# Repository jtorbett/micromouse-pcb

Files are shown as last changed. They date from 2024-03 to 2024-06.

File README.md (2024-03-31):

# Micromouse code

*A maze-solving micromouse implemented on STM32F446RE*

This mouse design has two DC motors driven by a TI DRV8833, and 4 IR sensors, two looking forward at an outward angle and two looking sideways, again at an angle.
Odometry is provided by a hall effect quadrature encoder on each motor.
Provision is made for a TDK ICM-42688 IMU, or a TDK ICM-45688 if and when that becomes available.
A forward-facing VL53L4CD time-of-flight ranging sensor is used for look-ahead

## Pin Descriptions

| STM32F446RE Pin number | Configuration | Name | Description |
|---|---|---|---|
| | PWM Output | LMotor_A | Left motor PWM signal 1 |
| | PWM Output | LMotor_B | Left motor PWM signal 2 |
| | PWM Output | RMotor_A | Right motor PWM signal 1 |
| | PWM Output | RMotor_B | Right motor PWM signal 2 |
| | GPIO Output | Motors_EN | DRM8833 Enable line |
| | GPIO Output | IR_Front_L_Pulse | Front left IR emitter pulse enable |
| | GPIO Output | IR_Front_R_Pulse | Front right IR emitter pulse enable |
| | GPIO Output | IR_L_Pulse | Left IR emitter pulse enable |
| | GPIO Output | IR_R_Pulse | Right IR emitter pulse enable |
| | ADC | IR_Front_L | Front Left IR Sensor |
| | ADC | IR_Front_R | Front Right IR Sensor |
| | ADC | IR_L | Left IR Sensor |
| | ADC | IR_R | Right IR Sensor |
| | Interrupt Input | L_ENC_A | Left encoder channel A |
| | Interrupt Input | L_ENC_B | Left encoder channel B |
| | Interrupt Input | R_ENC_A | Right encoder channel A |
| | Interrupt Input | R_ENC_B | Right encoder channel B |
| | I2C SDA | VL53L4CD_SDA | I2C bus data for VL53L4CD |
| | I2C SCL | VL53L4CD_SCL | I2C bus clock for VL53L4CD |
| | Interrupt Input | VL53L4CD_INT | Interrupt from VL53L4CD |
| | GPIO Output | VL53L4CD_EN | Enable for VL53L4CD |
| | SPI SCK | ICM-42688_SCK | SPI Clock for ICM-42688 |
| | SPI MISO | ICM-42688_MISO | SPI MISO for ICM-42688 |
| | SPI MOSI | ICM-42688_MOSI | SPI MOSI for ICM-42688 |
| | SPI CS or GPIO Output | ICM-42688_CS | Chip select, active low, for ICM-42688 |
| | GPIO Interrupt | ICM-42688_INT1 | Interrupt 1 from ICM-42688 |
| | GPIO Interrupt | ICM-42688_INT2 | Interrupt 2 from ICM-42688 |
| | GPIO Input or Interrupt | SW1 | Switch 1, momentary push-button input |
| | GPIO Input or Interrupt | SW2 | Switch 2, momentary push-button input |
| | GPIO Output | LED1 | LED 1 Output |
| | GPIO Output | LED2 | LED 2 Output |
| | ADC | VBATT | Battery voltage input |
| | SWDIO | SWDIO | Serial Wire Debug Data |
| | SWDCLK | SWDCLK | Serial Wire Debug Clock |

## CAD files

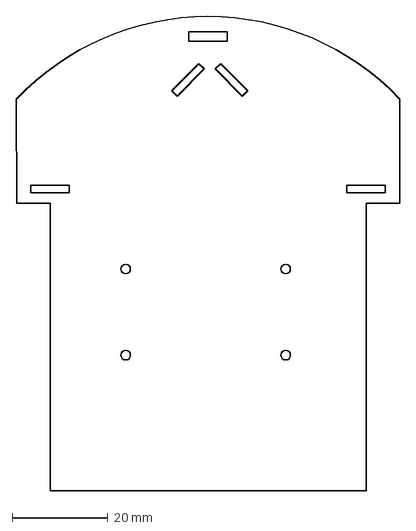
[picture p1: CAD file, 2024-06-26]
micromouse-pcb/outline.dxf
80.0 x 99.0 mm

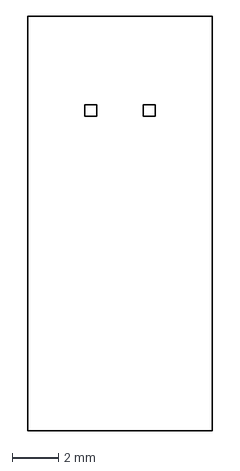
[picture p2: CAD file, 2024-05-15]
micromouse-pcb/sensor-outline.dxf
8.00 x 18.0 mm

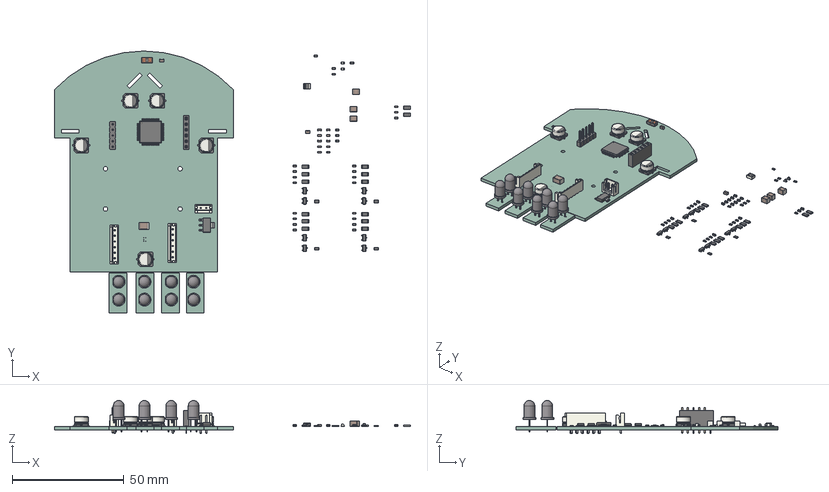
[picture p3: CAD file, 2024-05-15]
micromouse-pcb/micromouse-pcb.step
159.4 x 117.3 x 14.8 mm
SOT_23 x 8
R_0603_1608Metric x 21
R_1206_3216Metric x 14
CP_Elec_63x45 x 5
C_0603_1608Metric x 15
R_0805_2012Metric x 4
ST_VL53L1x
C_1210_3225Metric x 3
LED_D5.0mm_IRGrey x 8
PinHeader_1x05_P254mm_Vertical
Fuse_1210_3225Metric
LED_0603_1608Metric x 2
C_0805_2012Metric x 2
LQFP_64_10x10mm_P05mm
C_1812_4532Metric
JST_B2B_EH_A
SOT_223
JST_B6B_EH_A x 2
PinSocket_1x06_P254mm_Vertical
_autosave-micromouse-pcb_PCB_1
_autosave-micromouse-pcb_PCB_2
_autosave-micromouse-pcb_PCB_3
_autosave-micromouse-pcb_PCB_4
_autosave-micromouse-pcb_PCB_5

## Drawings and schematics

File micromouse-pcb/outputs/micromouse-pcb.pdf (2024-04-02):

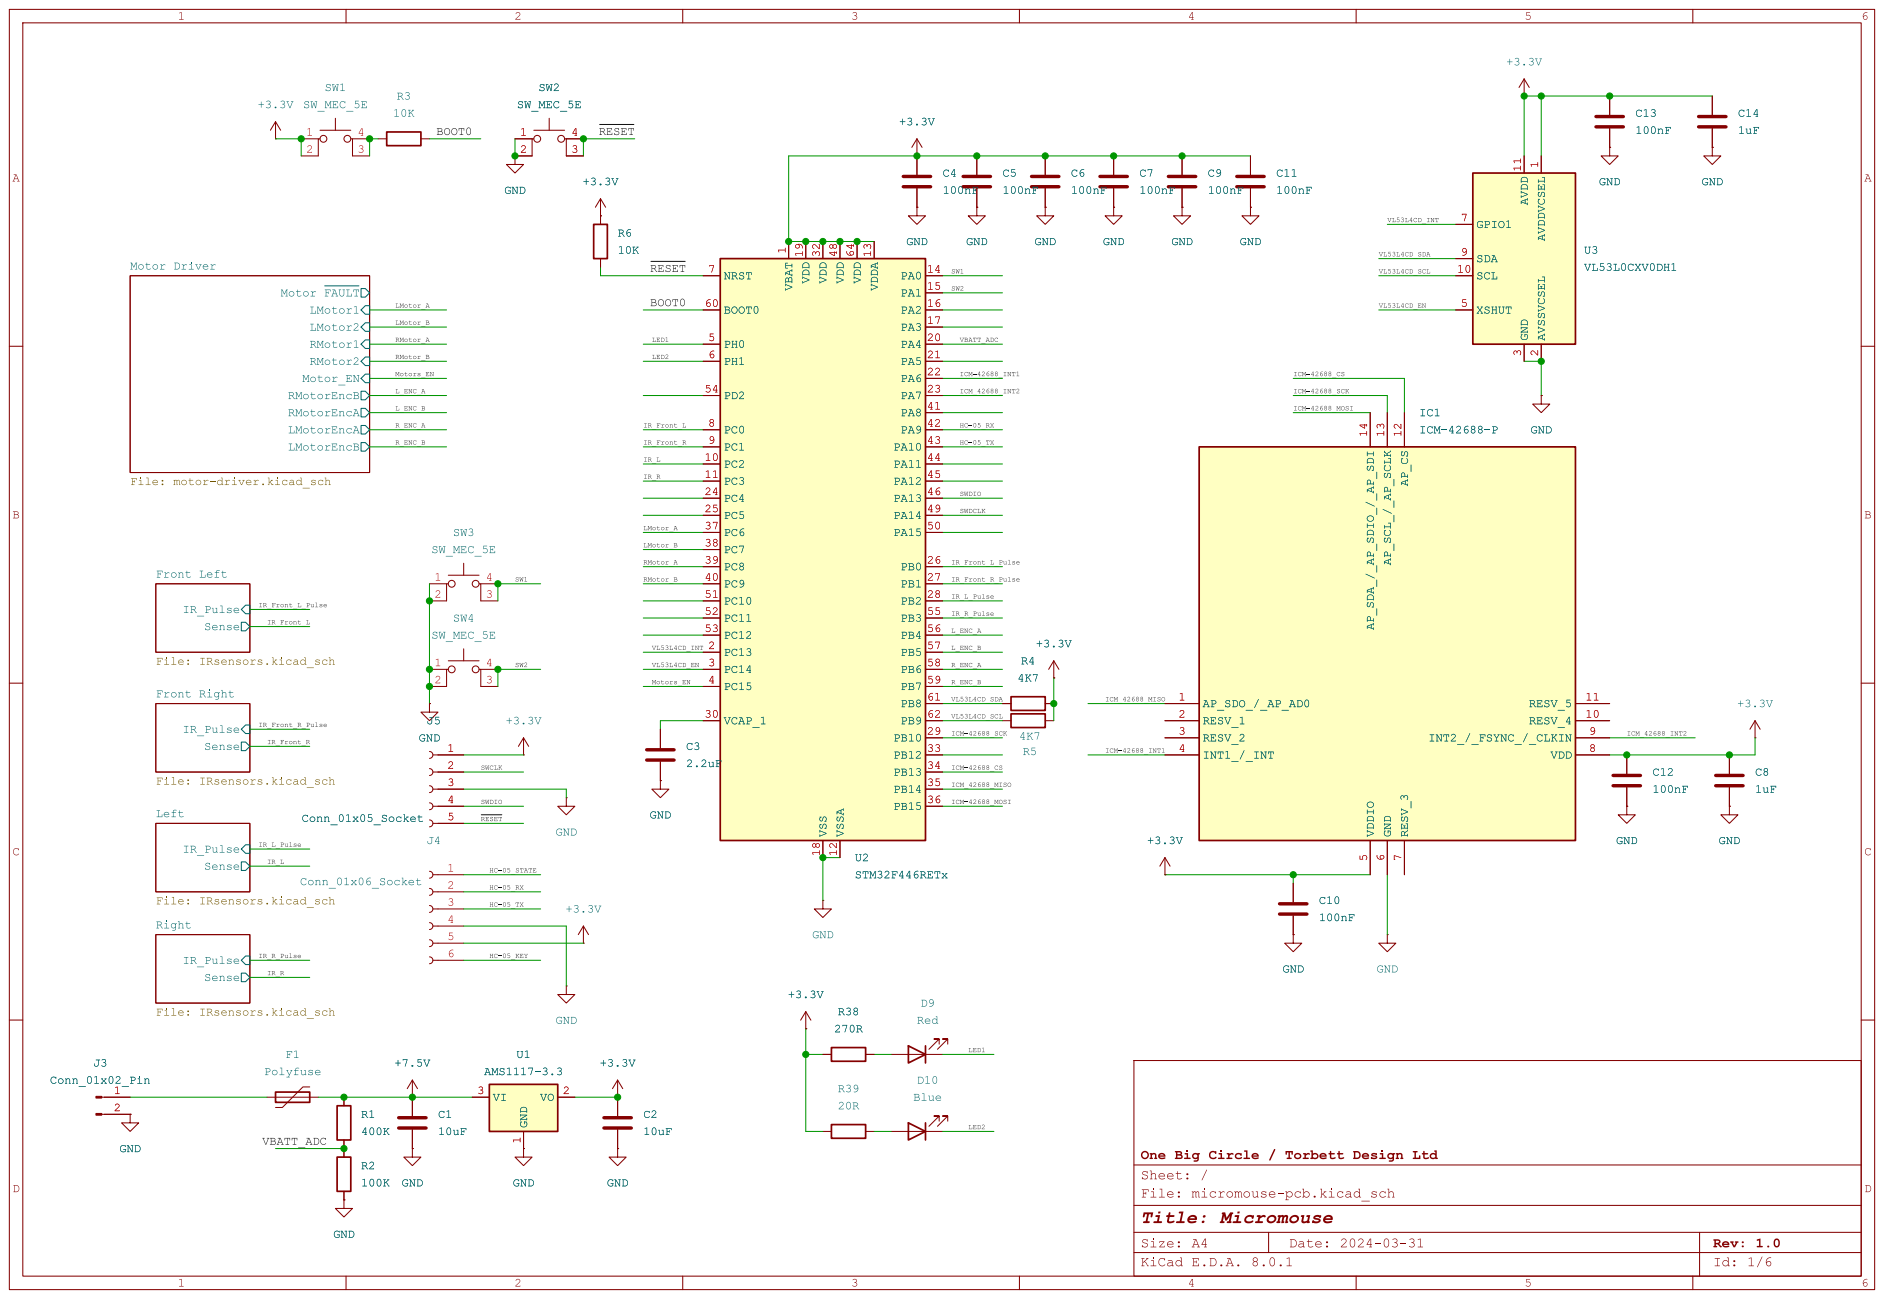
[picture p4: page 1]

1 PC2 10 PC3 11 VSSA 12 VDDA13 PA0 14 PA1 15 PA2 16 PA3 17 VSS 18 VDD19 PC13 2 PA4 20 PA5 21 PA6 22 PA7 23 PC4 24 PC5 25 PB0 26 PB1 27 PB2 28 PB10 29 PC14 3 VCAP_1 30 VDD32 PB12 33 PB13 34 PB14 35 PB15 36 PC6 37 PC7 38 PC8 39 PC15 4 PC9 40 PA8 41 PA9 42 PA10 43 PA11 44 PA12 45 PA13 46 VDD48 PA14 49 PH0 5 PA15 50 PC10 51 PC11 52 PC12 53 PD2 54 PB3 55 PB4 56 PB5 57 PB6 58 PB7 59 PH1 6 BOOT0 60 PB8 61 PB9 62 VDD64 NRST 7 PC0 8 PC1 9 GND
IR_L ~{RESET}

1 PC2 10 PC3 11 VSSA 12 VDDA13 PA0 14 PA1 15 PA2 16 PA3 17 VSS 18 VDD19 PC13 2 PA4 20 PA5 21 PA6 22 PA7 23 PC4 24 PC5 25 PB0 26 PB1 27 PB2 28 PB10 29 PC14 3 VCAP_1 30 VDD32 PB12 33 PB13 34 PB14 35 PB15 36 PC6 37 PC7 38 PC8 39 PC15 4 PC9 40 PA8 41 PA9 42 PA10 43 PA11 44 PA12 45 PA13 46 VDD48 PA14 49 PH0 5 PA15 50 PC10 51 PC11 52 PC12 53 PD2 54 PB3 55 PB4 56 PB5 57 PB6 58 PB7 59 PH1 6 BOOT0 60 PB8 61 PB9 62 VDD64 NRST 7 PC0 8 PC1 9 U2STM32F446RETx GND

ICM-42688_MOSI HC-05_STATE HC-05_RX HC-05_KEY

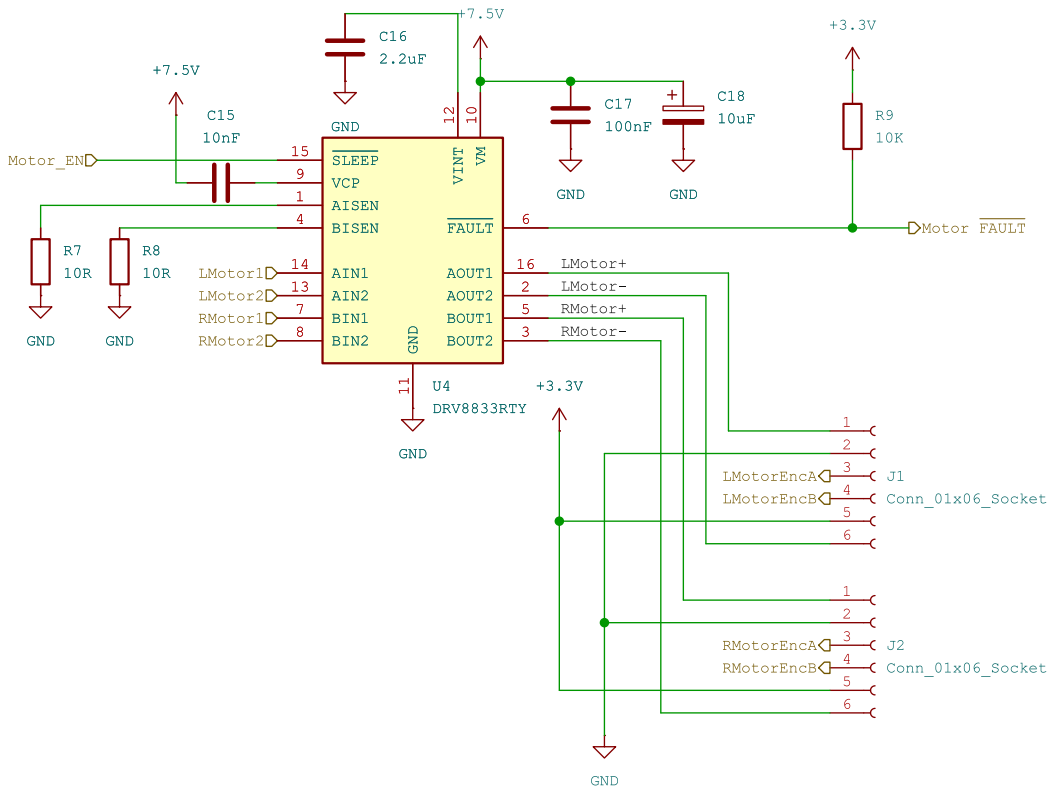
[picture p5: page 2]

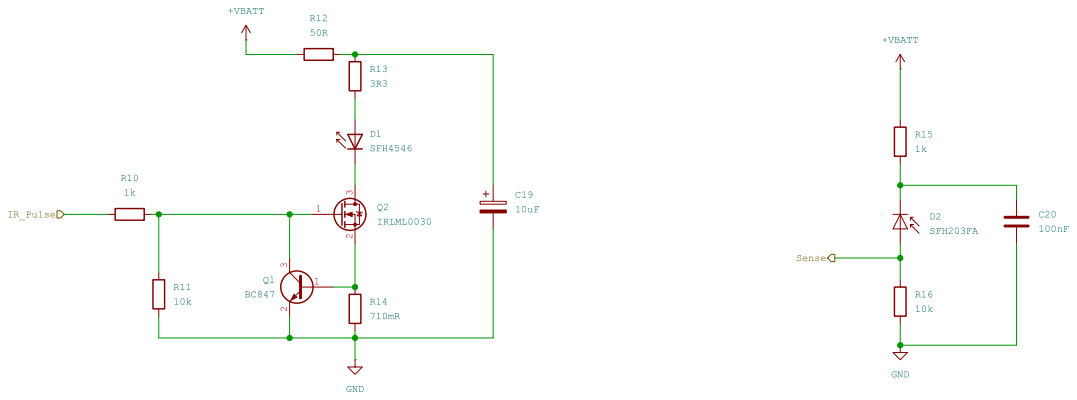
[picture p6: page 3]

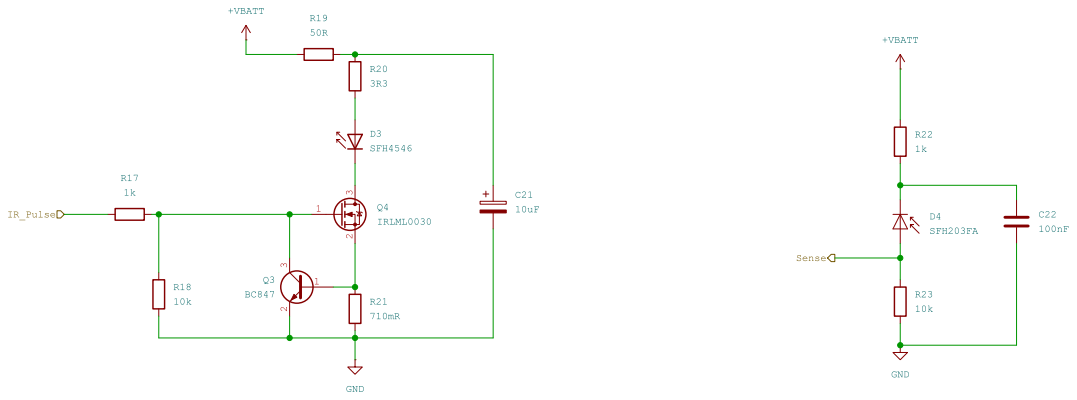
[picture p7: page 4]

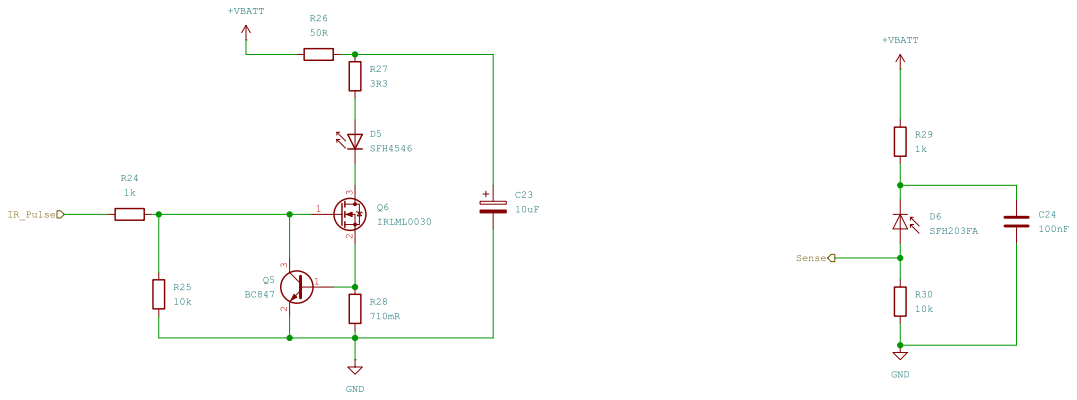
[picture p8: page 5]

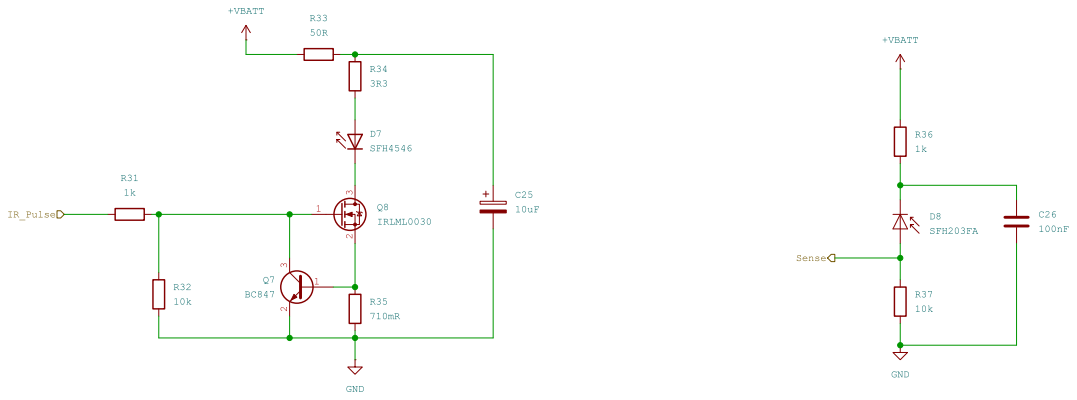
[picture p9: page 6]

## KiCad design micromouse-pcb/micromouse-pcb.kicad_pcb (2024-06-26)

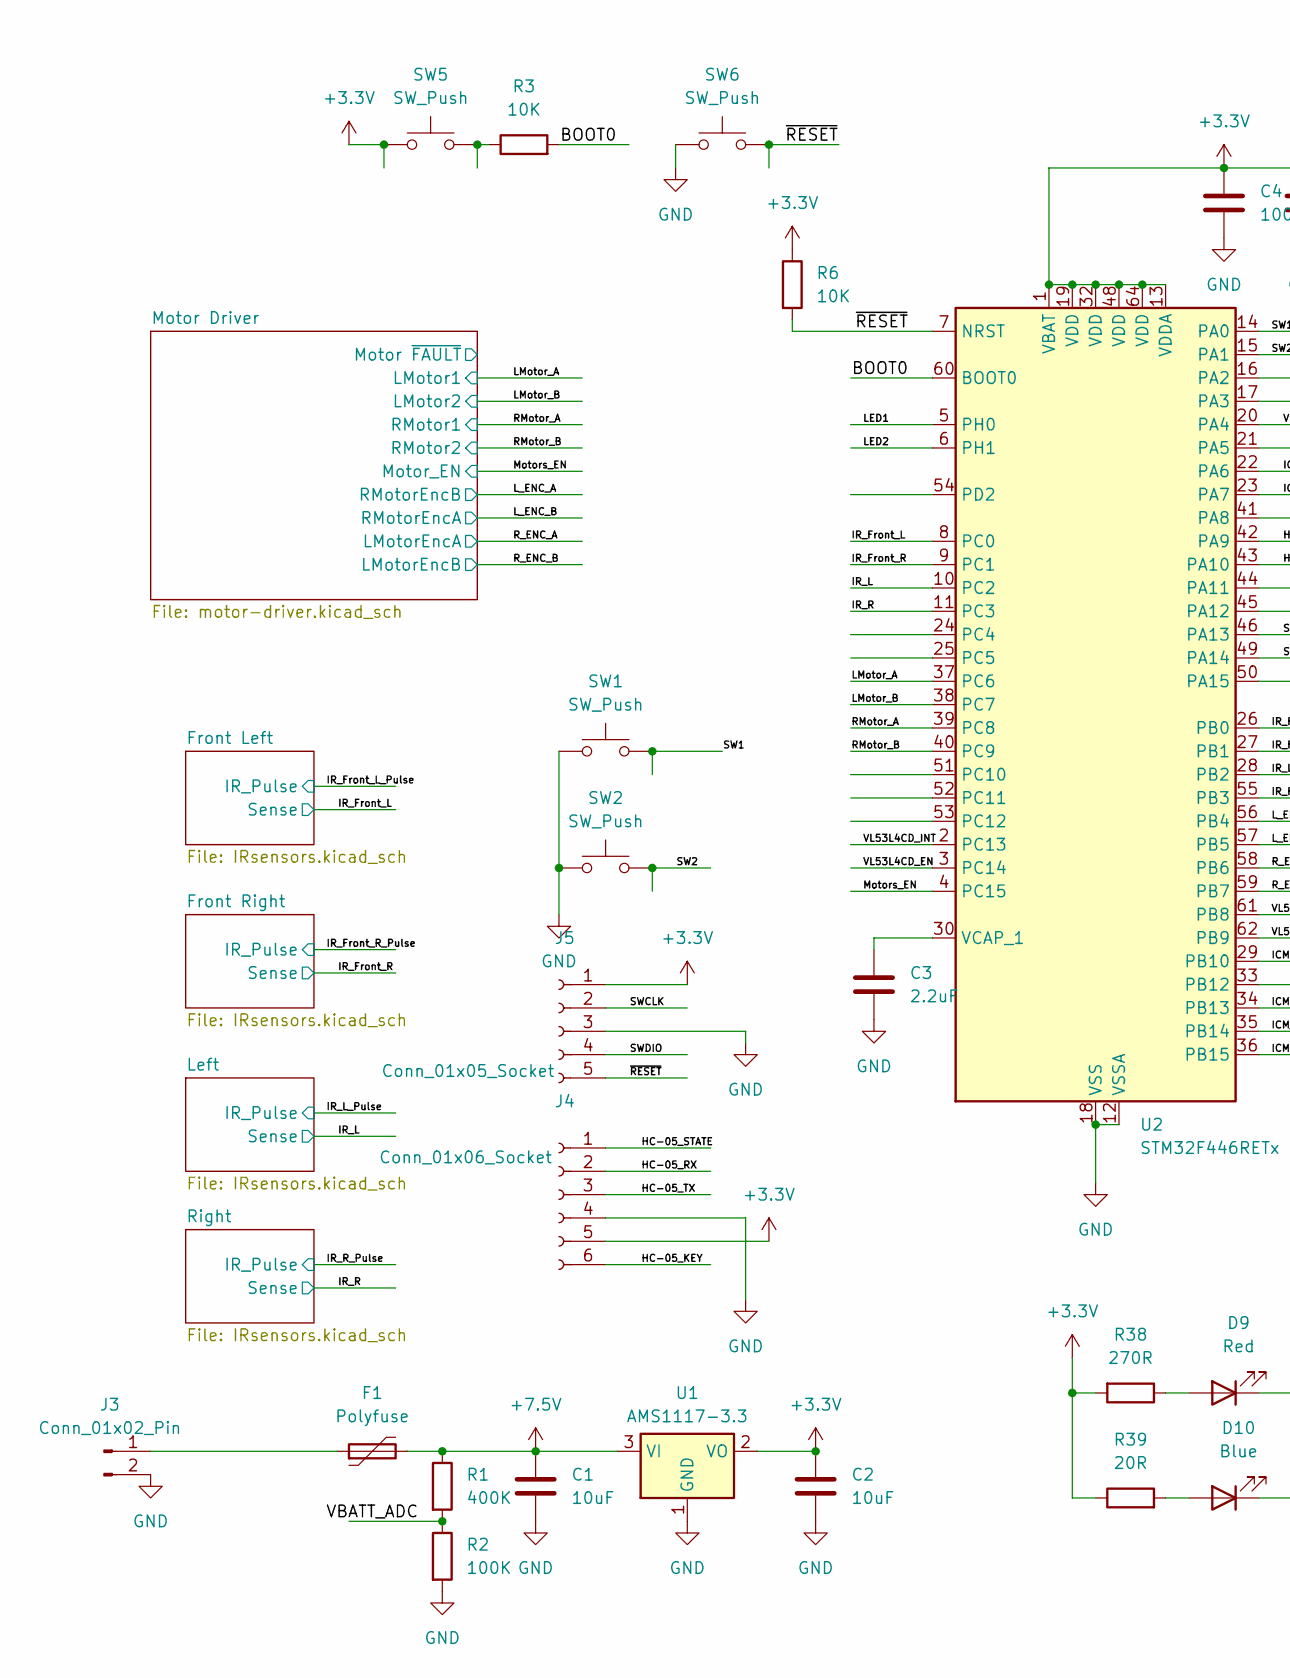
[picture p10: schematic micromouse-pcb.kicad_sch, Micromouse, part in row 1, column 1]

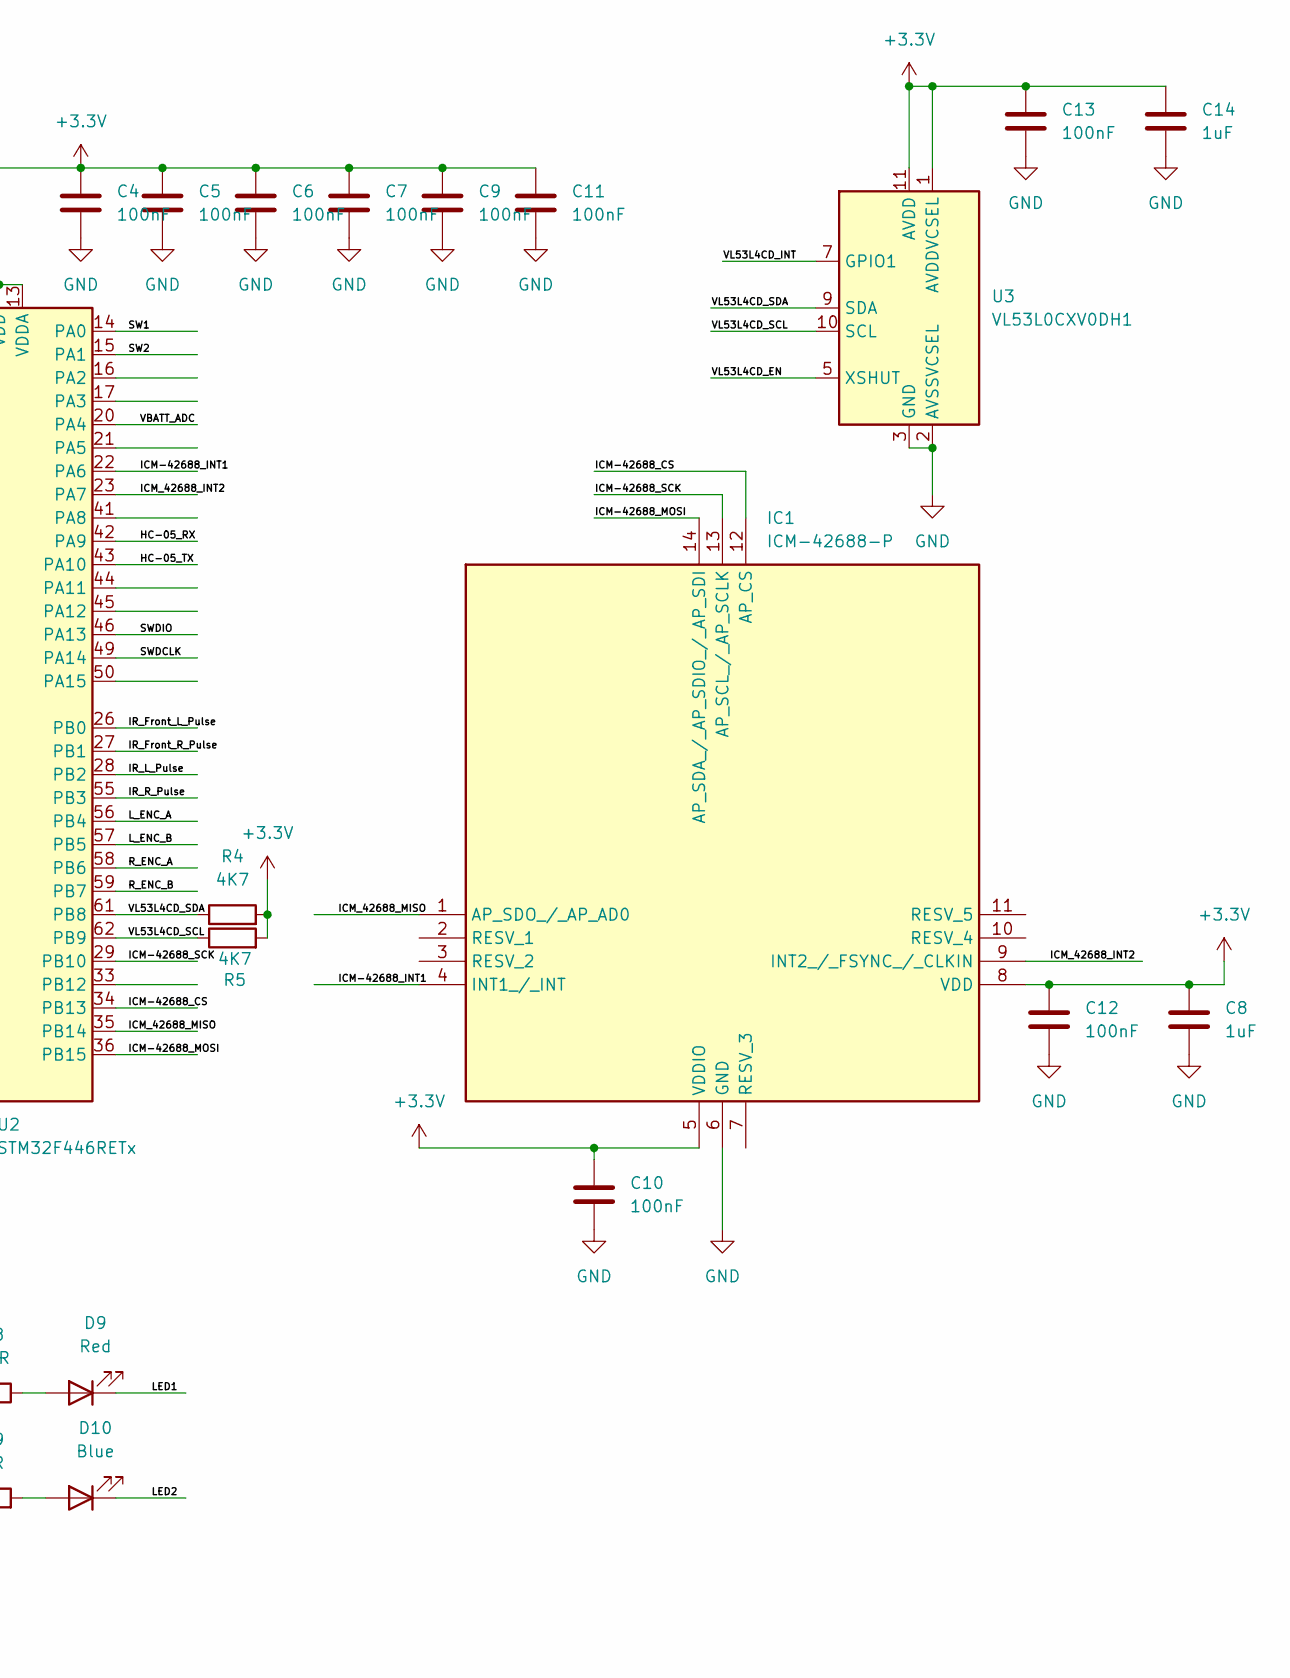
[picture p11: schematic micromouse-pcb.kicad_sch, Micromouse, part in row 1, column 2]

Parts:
C1, C2: 10uF; C_1210_3225Metric
C3: 2.2uF; C_1210_3225Metric
C4, C5, C6, C7, C9, C11, C12, C13: 100nF; C_0603_1608Metric
C8: 1uF; C_0603_1608Metric
C10: 100nF; C_0805_2012Metric
C14: 1uF; C_0805_2012Metric
D9: Red; LED_0603_1608Metric
D10: Blue; LED_0603_1608Metric
F1: Polyfuse; Fuse_1210_3225Metric
IC1: ICM-42688-P; IIM42352; Mouser Part Number 410-ICM-42688-P
J3: Conn_01x02_Pin; JST_EH_B2B-EH-A_1x02_P2.50mm_Vertical
J4: Conn_01x06_Socket; PinSocket_1x06_P2.54mm_Vertical
J5: Conn_01x05_Socket; PinHeader_1x05_P2.54mm_Vertical
R1: 400K; R_0603_1608Metric
R2: 100K; R_0603_1608Metric
R3, R6: 10K; R_0603_1608Metric
R4, R5: 4K7; R_0603_1608Metric
R38: 270R; R_0603_1608Metric_Pad0.98x0.95mm_HandSolder
R39: 20R; R_0603_1608Metric
SW1, SW2, SW5, SW6: SW_Push; SW_Push_1P1T_NO_CK_KSC6xxJ
U1: AMS1117-3.3; SOT-223-3_TabPin2
U2: STM32F446RETx; LQFP-64_10x10mm_P0.5mm
U3: VL53L0CXV0DH1; ST_VL53L1x

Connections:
+3.3V: C2.1, C4.1, C5.1, C6.1, C7.1, C8.1, C9.1, C10.1, C11.1, C12.1, C13.1, C14.1, IC1.5 (VDDIO), IC1.8 (VDD), J4.5, J5.1, R4.2, R5.2, R6.1, R38.2, R39.1, SW5.1, U1.2 (VO), U2.1 (VBAT), U2.13 (VDDA), U2.19 (VDD), U2.32 (VDD), U2.48 (VDD), U2.64 (VDD), U3.1 (AVDDVCSEL), U3.11 (AVDD); also elsewhere on the board
+7.5V: C1.1, F1.2, R1.1, U1.3 (VI); also elsewhere on the board
/BOOT0: R3.2, U2.60 (BOOT0)
/HC-05_KEY: J4.6
/HC-05_RX: J4.2, U2.42 (PA9)
/HC-05_STATE: J4.1
/HC-05_TX: J4.3, U2.43 (PA10)
/ICM-42688_CS: IC1.12 (AP_CS), U2.34 (PB13)
/ICM-42688_INT1: IC1.4 (INT1_/_INT), U2.22 (PA6)
/ICM-42688_MOSI: IC1.14 (AP_SDA_/_AP_SDIO_/_AP_SDI), U2.36 (PB15)
/ICM-42688_SCK: IC1.13 (AP_SCL_/_AP_SCLK), U2.29 (PB10)
/ICM_42688_INT2: IC1.9 (INT2_/_FSYNC_/_CLKIN), U2.23 (PA7)
/ICM_42688_MISO: IC1.1 (AP_SDO_/_AP_AD0), U2.35 (PB14)
/IR_Front_L: U2.8 (PC0); also elsewhere on the board
/IR_Front_L_Pulse: U2.26 (PB0); also elsewhere on the board
/IR_Front_R: U2.9 (PC1); also elsewhere on the board
/IR_Front_R_Pulse: U2.27 (PB1); also elsewhere on the board
/IR_L: U2.10 (PC2); also elsewhere on the board
/IR_L_Pulse: U2.28 (PB2); also elsewhere on the board
/IR_R: U2.11 (PC3); also elsewhere on the board
/IR_R_Pulse: U2.55 (PB3); also elsewhere on the board
/LED1: D9.1 (K), U2.5 (PH0)
/LED2: D10.1 (K), U2.6 (PH1)
/LMotor_A: U2.37 (PC6); also elsewhere on the board
/LMotor_B: U2.38 (PC7); also elsewhere on the board
/L_ENC_A: U2.56 (PB4); also elsewhere on the board
/L_ENC_B: U2.57 (PB5); also elsewhere on the board
/Motors_EN: U2.4 (PC15); also elsewhere on the board
/RMotor_A: U2.39 (PC8); also elsewhere on the board
/RMotor_B: U2.40 (PC9); also elsewhere on the board
/R_ENC_A: U2.58 (PB6); also elsewhere on the board
/R_ENC_B: U2.59 (PB7); also elsewhere on the board
/SW1: SW1.2, U2.14 (PA0)
/SW2: SW2.2, U2.15 (PA1)
/SWCLK: J5.2
/SWDCLK: U2.49 (PA14)
/SWDIO: J5.4, U2.46 (PA13)
/VBATT_ADC: R1.2, R2.1, U2.20 (PA4)
/VL53L4CD_EN: U2.3 (PC14), U3.5 (XSHUT)
/VL53L4CD_INT: U2.2 (PC13), U3.7 (GPIO1)
/VL53L4CD_SCL: R5.1, U2.62 (PB9), U3.10 (SCL)
/VL53L4CD_SDA: R4.1, U2.61 (PB8), U3.9 (SDA)
/~RESET: J5.5, R6.2, SW6.2, U2.7 (NRST)
GND: C1.2, C2.2, C3.2, C4.2, C5.2, C6.2, C7.2, C8.2, C9.2, C10.2, C11.2, C12.2, C13.2, C14.2, IC1.6 (GND), J3.2, J4.4, J5.3, R2.2, SW1.1, SW2.1, SW6.1, U1.1 (GND), U2.12 (VSSA), U2.18 (VSS), U2.31 (VSS), U2.47 (VSS), U2.63 (VSS), U3.2 (AVSSVCSEL), U3.3 (GND), U3.4 (GND), U3.6 (GND), U3.12 (GND); also elsewhere on the board
unnamed: D9.2 (A), R38.1
unnamed: D10.2 (A), R39.2
unnamed: F1.1, J3.1
unnamed: R3.1, SW5.2
unnamed: C3.1, U2.30 (VCAP_1)

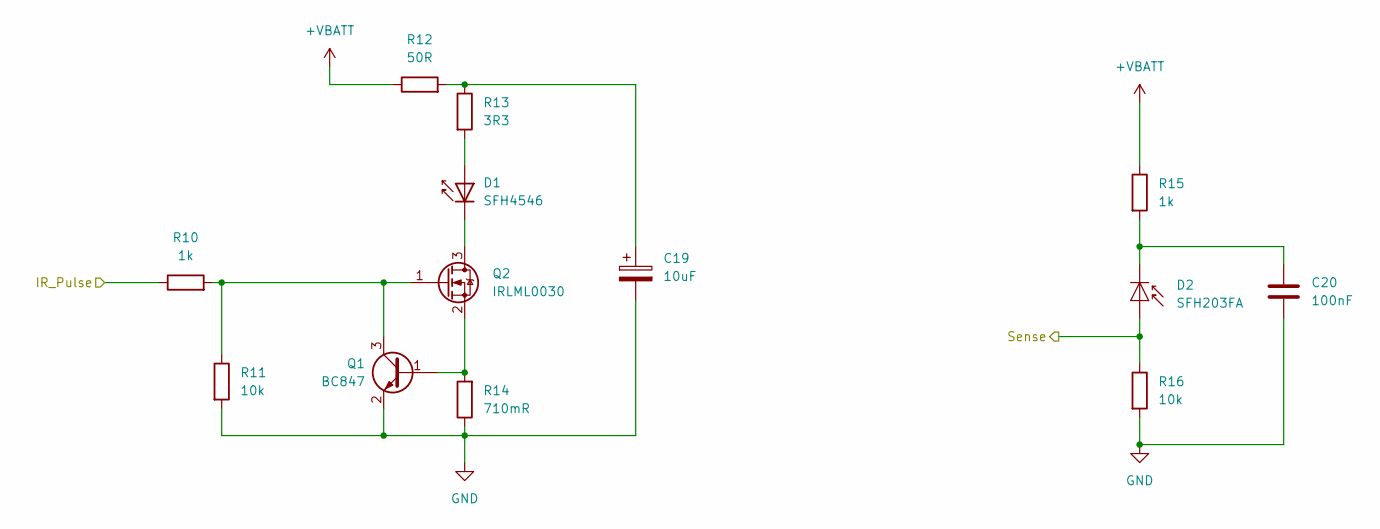
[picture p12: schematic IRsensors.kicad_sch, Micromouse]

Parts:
C19: 10uF; CP_Elec_6.3x4.5
C20: 100nF; C_0603_1608Metric
D1: SFH4546; LED_D5.0mm_IRGrey
D2: SFH203FA; LED_D5.0mm_IRGrey
Q1: BC847; SOT-23
Q2: IRLML0030; SOT-23
R10: 1k; R_0603_1608Metric
R11, R16: 10k; R_0603_1608Metric
R12: 50R; R_1206_3216Metric
R13: 3R3; R_1206_3216Metric
R14: 710mR; R_1206_3216Metric
R15: 1k; R_0805_2012Metric

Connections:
+VBATT: R12.1, R15.1; also elsewhere on the board
/IR_Front_R: D2.2 (A), R16.1; also elsewhere on the board
/IR_Front_R_Pulse: R10.1; also elsewhere on the board
GND: C19.2, C20.2, Q1.2 (E), R11.2, R14.1, R16.2; also elsewhere on the board
unnamed: C19.1, R12.2, R13.1
unnamed: D1.2 (A), R13.2
unnamed: D1.1 (K), Q2.3 (D)
unnamed: C20.1, D2.1 (K), R15.2
unnamed: Q1.1 (B), Q2.2 (S), R14.2
unnamed: Q1.3 (C), Q2.1 (G), R10.2, R11.1

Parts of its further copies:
C21, C23, C25: 10uF; CP_Elec_6.3x4.5
C22, C24, C26: 100nF; C_0603_1608Metric
D3, D5, D7: SFH4546; LED_D5.0mm_IRGrey
D4, D6, D8: SFH203FA; LED_D5.0mm_IRGrey
Q3, Q5, Q7: BC847; SOT-23
Q4, Q6, Q8: IRLML0030; SOT-23
R17, R24, R31: 1k; R_0603_1608Metric
R18, R23, R25, R30, R32, R37: 10k; R_0603_1608Metric
R19, R26, R33: 50R; R_1206_3216Metric
R20, R27, R34: 3R3; R_1206_3216Metric
R21, R28, R35: 710mR; R_1206_3216Metric
R22, R29, R36: 1k; R_0805_2012Metric

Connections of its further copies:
+VBATT: R19.1, R22.1, R26.1, R29.1, R33.1, R36.1; also elsewhere on the board
/IR_Front_L: D6.2 (A), R30.1; also elsewhere on the board
/IR_Front_L_Pulse: R24.1; also elsewhere on the board
/IR_L: D4.2 (A), R23.1; also elsewhere on the board
/IR_L_Pulse: R17.1; also elsewhere on the board
/IR_R: D8.2 (A), R37.1; also elsewhere on the board
/IR_R_Pulse: R31.1; also elsewhere on the board
GND: C21.2, C22.2, C23.2, C24.2, C25.2, C26.2, Q3.2 (E), Q5.2 (E), Q7.2 (E), R18.2, R21.1, R23.2, R25.2, R28.1, R30.2, R32.2, R35.1, R37.2; also elsewhere on the board
unnamed: C21.1, R19.2, R20.1
unnamed: C23.1, R26.2, R27.1
unnamed: C25.1, R33.2, R34.1
unnamed: D3.2 (A), R20.2
unnamed: D3.1 (K), Q4.3 (D)
unnamed: C22.1, D4.1 (K), R22.2
unnamed: D5.2 (A), R27.2
unnamed: D5.1 (K), Q6.3 (D)
unnamed: C24.1, D6.1 (K), R29.2
unnamed: D7.2 (A), R34.2
unnamed: D7.1 (K), Q8.3 (D)
unnamed: C26.1, D8.1 (K), R36.2
unnamed: Q3.1 (B), Q4.2 (S), R21.2
unnamed: Q3.3 (C), Q4.1 (G), R17.2, R18.1
unnamed: Q5.1 (B), Q6.2 (S), R28.2
unnamed: Q5.3 (C), Q6.1 (G), R24.2, R25.1
unnamed: Q7.1 (B), Q8.2 (S), R35.2
unnamed: Q7.3 (C), Q8.1 (G), R31.2, R32.1

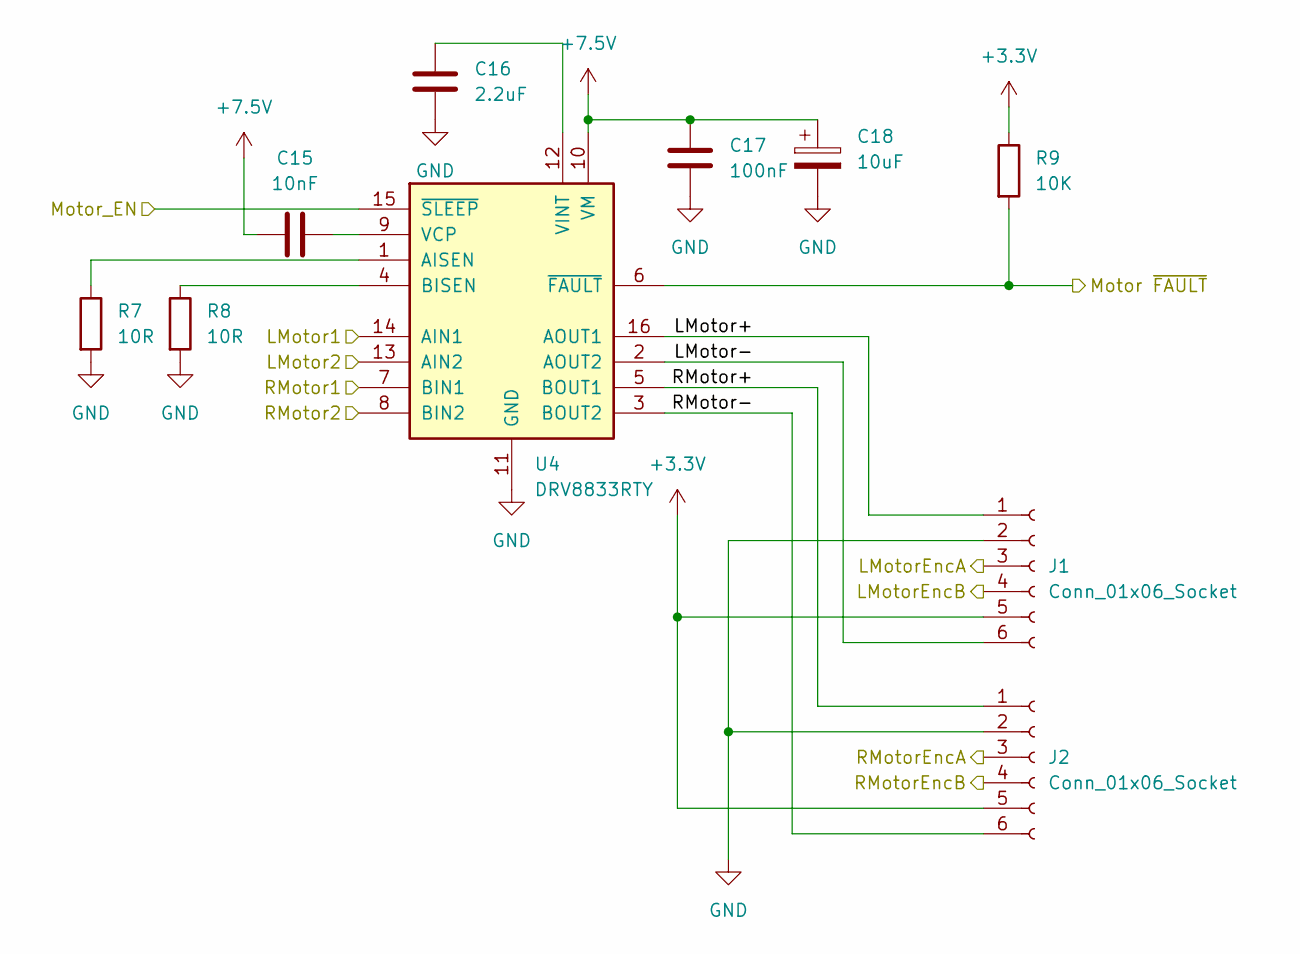
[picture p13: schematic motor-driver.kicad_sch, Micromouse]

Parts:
C15: 10nF; C_0603_1608Metric
C16: 2.2uF; C_1812_4532Metric
C17: 100nF; C_0603_1608Metric
C18: 10uF; CP_Elec_6.3x4.5
J1, J2: Conn_01x06_Socket; JST_EH_B6B-EH-A_1x06_P2.50mm_Vertical
R7, R8: 10R; R_1206_3216Metric
R9: 10K; R_0603_1608Metric
U4: DRV8833RTY; Texas_RTY_WQFN-16-1EP_4x4mm_P0.65mm_EP2.1x2.1mm_ThermalVias

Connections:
+3.3V: J1.5, J2.5, R9.1; also elsewhere on the board
+7.5V: C15.1, C17.1, C18.1, U4.10 (VM); also elsewhere on the board
/LMotor_A: U4.14 (AIN1); also elsewhere on the board
/LMotor_B: U4.13 (AIN2); also elsewhere on the board
/L_ENC_A: J2.4; also elsewhere on the board
/L_ENC_B: J2.3; also elsewhere on the board
/Motor Driver/LMotor+: J1.1, U4.16 (AOUT1)
/Motor Driver/LMotor-: J1.6, U4.2 (AOUT2)
/Motor Driver/Motor ~FAULT: R9.2, U4.6 (~FAULT)
/Motor Driver/RMotor+: J2.1, U4.5 (BOUT1)
/Motor Driver/RMotor-: J2.6, U4.3 (BOUT2)
/Motors_EN: U4.15 (~SLEEP); also elsewhere on the board
/RMotor_A: U4.7 (BIN1); also elsewhere on the board
/RMotor_B: U4.8 (BIN2); also elsewhere on the board
/R_ENC_A: J1.3; also elsewhere on the board
/R_ENC_B: J1.4; also elsewhere on the board
GND: C16.2, C17.2, C18.2, J1.2, J2.2, R7.2, R8.2, U4.11 (GND), U4.17 (GND); also elsewhere on the board
unnamed: R7.1, U4.1 (AISEN)
unnamed: R8.1, U4.4 (BISEN)
unnamed: C15.2, U4.9 (VCP)
unnamed: C16.1, U4.12 (VINT)

Board: 2 copper layers, 98 parts (0 on the bottom side), 79 nets, no tracks yet.

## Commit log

2024-03-31 Initial commit - basic schematic done but need pin assignments
    [IRsensors.kicad_sch, micromouse-pcb.kicad_pcb, micromouse-pcb.kicad_sch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]
2024-04-02 Finalised schematic
    [IRsensors.kicad_sch, micromouse-pcb.kicad_sch, motor-driver.kicad_sch]
2024-05-15 Updated schematics and brought in board shape from CAD
    [IRsensors.kicad_sch, micromouse-pcb.kicad_pcb, micromouse-pcb.kicad_sch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]
2024-06-26 Updated outline and PCB file
    [micromouse-pcb.kicad_pcb, outline.dxf]
